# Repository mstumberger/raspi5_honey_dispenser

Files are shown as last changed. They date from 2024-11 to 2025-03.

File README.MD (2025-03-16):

# Raspberry PI 5 honey dispenser

# Material

| Part | Price  | URL |
|---|---|---|
| 3D printed parts | ~5€ | https://github.com/mstumberger/raspi5_honey_dispenser/tree/master/stl |
| Raspberry pi 5 | 76.19€ | https://si.farnell.com/raspberry-pi/rpi5-8gb-single/raspberry-pi-5-model-b-8gb-2-4ghz/dp/4256000 |
| MicroSD card 32GB | 12.90€ | https://si.farnell.com/multicomp-pro/ts32gusd420t-mcp/mircosd-card-32gb-raspberry-pi/dp/3879376  |
| Power supply | 12.48€ | https://si.farnell.com/raspberry-pi/sc1157/power-supply-usb-c-5-1v-5a-black/dp/4263045 |
| USB Extension cable 0.3m | 6.5€ | https://www.aliexpress.com/item/1005003488021890.html |
| 5" touch screen | 27.94€ | https://www.aliexpress.com/item/1005007314274603.html |
| 90° HDMI cable (conn. A2, D2, cable 30cm) | 9.09€  | https://www.aliexpress.com/item/1005005945873056.html |
| 90° USB cable (AMUP-V8UP, 30CM) | 6.57€  | https://www.aliexpress.com/item/1005005978243043.html |
| 5kg Load Cell with HX711 Amplifier | 5.75€  | https://www.aliexpress.com/item/1005005990685261.html |
| 10x 2.54MM Pitch 30CM Dupont Line Wire | 3.19€  | https://www.aliexpress.com/item/1005005924705004.html |
| Connectors for motor connection | 5.21€  | https://www.aliexpress.com/item/1005004891694780.html |
| Connection wire 22AWG (1/3) | 6.08€  | https://www.aliexpress.com/item/1005006516374385.html |
| MG996R Servo motor | 5.35€  | https://www.aliexpress.com/item/1005007552788835.html |
| Piezzo buzzer | 0.23€  | https://www.aliexpress.com/item/1005006260328559.html |
| PWM Cooling Fan | 7.86€  | https://www.aliexpress.com/item/1005004219041650.html |
| RGB LED | 0.04€  | https://www.aliexpress.com/item/1005005990835193.html |
| SMD R150 and 2x R33 | 0.01€  | https://www.aliexpress.com/item/1005006823361841.html |
| PCB Proto-board | 0.30€  | https://www.aliexpress.com/item/1005006665029598.html | 
| 8x M2.5 Brass Hot Melt Nut Insert + bolt  | ~0.18€ | https://www.aliexpress.com/item/1005006760493119.html |

Total costs:

    ~190.87€

# Wiring

-	HX711 - GND 39, VCC 17, DT 40, SCK 38 (Weight)
-	Servo - GND 6, VCC 2, Signal 12 (Dosing)
-	Fan - GND 9, VCC 4 (PWM fan)	
-   Piezzo - Signal 36 (Audio Signal)
-	RGB LED - GND 14, Green 16, Blue 15, Red 13

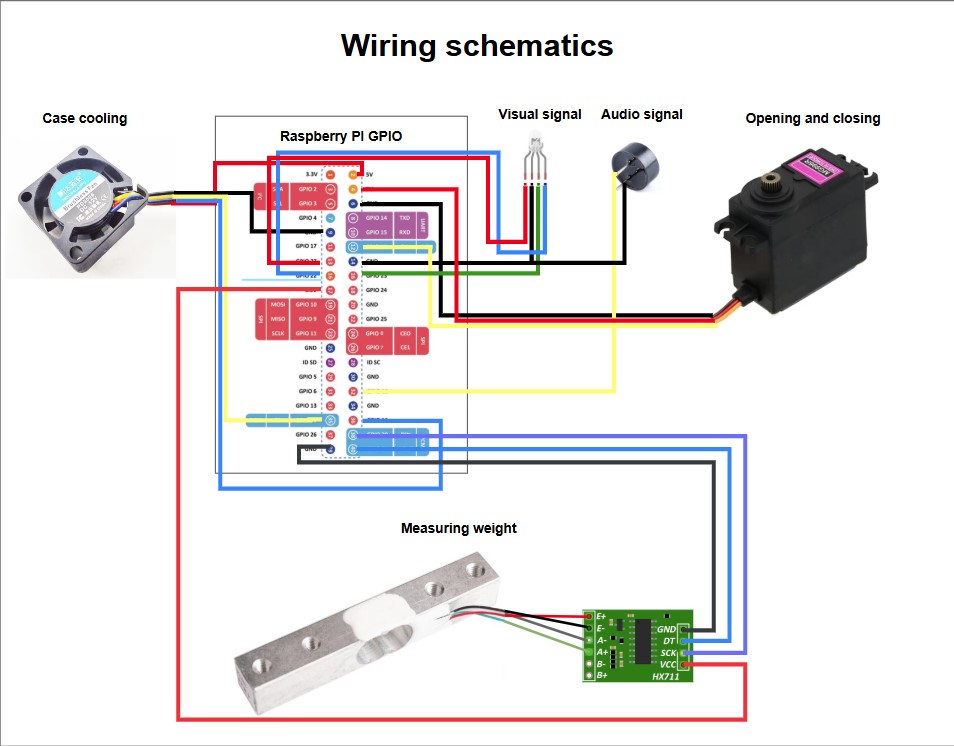
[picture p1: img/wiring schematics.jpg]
schematics


# Assembly instructions

1. Print STL Files for all components.
2. Insert Brass Insert Nuts into mounting locations on Raspberry Pi 5, signalization proto-board, HX711 amplifier, and display holder.
3. Solder Components: Attach the Piezo and RGB LED to the proto-board, create a common ground, and use connectors for wiring to the Raspberry Pi.
4. Mount Touchscreen: Connect the USB and HDMI cables to the touchscreen, then mount it onto the "stl/Scale - Display holder v5.stl" using 4 M2.5 screws.
5. Prepare Servo Motor Wiring: Solder 3 wires to a male connector for controlling the servo motor, then place the connector into the display holder.
6. Install USB-C Extension: Mount the USB-C extension onto the display holder using provided screws.
7. Mount Load Cell: Attach the load cell to the display holder at the designated mounting point, ensuring the correct orientation. Also attach Scaling surface to the other end of the load cell.
8. Wire Connection: Route and connect the cables inside the housing to the HX711 amplifier, securing them with M2.5 screws.
9. Prepare MicroSD Card: Load Raspbian OS onto the microSD card and insert it into the Raspberry Pi card slot.
10. Install Raspberry Pi: Place the Raspberry Pi into its dedicated space in the holder and secure it with M2.5 screws. Connect the microHDMI and USB-C cables.
11. Connect Display Cables: Route the USB cable for the touch display through the designated space in the cover, then place the cover on the scale base, ensuring it clicks into place.
12. Power On: Connect the USB and power adapter to the scale, plug the power adapter into a socket, and wait for the Raspberry Pi to boot.
13. Prepare Servo Motor Cable: Solder two female connectors to the servo motor control cable.
14. Connect to Lid Adapter: Cut the servo motor wires, solder them to the male connector fixed in the "stl/Lid adapter - top.stl."
15. Attach Lid Adapter: Use two nuts and bolts to secure the lid adapter to the honey dispenser.
16. Install Servo Motor Handles: Attach the large handle to the servo motor adapter and secure it vertically. Fix the small handle by drilling a hole and using a screw.
17. Disconnect Large Handle for initial installation.
18. Motor Calibration: Once the application starts and the motor moves to position 0, reattach the large handle.
19. Calibrate Scale: Calibrate the scale using a known weight to ensure accuracy.
20. Start Honey Dispensing: Once calibration is complete and saved, you can begin dispensing honey

schematics

## Install
This script will automatically:
- apply patch for Raspberry PI 5 HX711 library,
- install dependencies,
- create desktop and menu entry and start the application

```console
pi@raspberrypi:~ $ git clone --depth=1 https://github.com/mstumberger/raspi5_honey_dispenser.git honey_dispenser
pi@raspberrypi:~ $ cd honey_dispenser
pi@raspberrypi:~/honey_dispenser $ chmod +x install_and_start.sh
pi@raspberrypi:~/honey_dispenser $ ./install_and_start.sh
```

## Manual Install

- Set rpi to performance mode:

```console
echo performance | sudo tee /sys/devices/system/cpu/cpu*/cpufreq/scaling_governor
```

- [lgpio-dev](http://abyz.me.uk/lg/index.html) is required to be installed. It may be available to you via apt:

```console
sudo apt-get install -y liblgpio-dev
```
If it is not available, manually build and install it by following the instructions [here](https://abyz.me.uk/lg/download.html#Download&Install).

- Install C++ dependency for python library

```console
pi@raspberrypi:~ $ git clone --depth=1 https://github.com/endail/hx711
pi@raspberrypi:~ $ cd hx711
```

For RPi 5 the expansion header GPIO pins are now on /dev/gpiochip4 instead of /dev/gpiochip0. [endail/hx711/issues/85](https://github.com/endail/hx711/issues/85#issuecomment-2129032985)

```console
pi@raspberrypi:~/hx711 $ cd src
pi@raspberrypi:~/hx711/src $ sed -i 's/Utility::openGpioHandle(0)/Utility::openGpioHandle(4)/g' HX711.cpp
pi@raspberrypi:~/hx711/src $ cd ..
```

```console
pi@raspberrypi:~/hx711 $ make && sudo make install
```

Source: [Raspberry Pi HX711 C++ Library Readme](https://github.com/endail/hx711/blob/master/README.md)

- clone application create virtual environment and install python dependencies

```console
pi@raspberrypi:~ $ git clone --depth=1 https://github.com/mstumberger/raspi5_honey_dispenser.git honey_dispenser
pi@raspberrypi:~ $ cd honey_dispenser
pi@raspberrypi:~/honey_dispenser $ python3 -m venv venv
pi@raspberrypi:~/honey_dispenser $ source venv/bin/activate
(venv) pi@raspberrypi:~/honey_dispenser $ pip3 install .
(venv) pi@raspberrypi:~/honey_dispenser $ deactivate
```

### Run

```console
pi@raspberrypi:~ $ honey_dispenser/venv/bin/dispenser
```

### Cooling Service

1. Create a Systemd Service

Copy service/fan_controller.service to /etc/systemd/system/fan_controller.service:
    
    sudo cp service/fan_controller.service /etc/systemd/system/fan_controller.service

2. Enable the Service

Run the following commands:

    sudo chmod +x /home/pi/fan_controller.py  # Ensure it's executable
    sudo systemctl daemon-reload  # Reload systemd
    sudo systemctl enable fan_controller.service  # Enable service on boot
    sudo systemctl start fan_controller.service  # Start the service now

3. Check if the service is running:

    sudo systemctl status fan_controller.service

Or to view live logs:

    journalctl -u fan_controller.service -f

### Tkiter application service

1. Create a Systemd Service

Copy service/tkinter_app.service to /etc/systemd/system/tkinter_app.service:

    sudo cp service/tkinter_app.service /etc/systemd/system/tkinter_app.service

2. Enable the Service

Run the following commands:

    sudo systemctl daemon-reload  # Reload systemd
    sudo systemctl enable tkinter_app.service  # Enable service on boot
    sudo systemctl start tkinter_app.service  # Start the service now

3. Check if the service is running:

    sudo systemctl status tkinter_app.service

Or to view live logs:

    journalctl -u tkinter_app.service -f

4. Stop running service:

    sudo systemctl stop tkinter_app.service

# Shutdown

To allow passwordless shutdown, you can edit the sudoers file:

    sudo visudo

Add the following line :

    pi ALL=(ALL) NOPASSWD: /sbin/shutdown

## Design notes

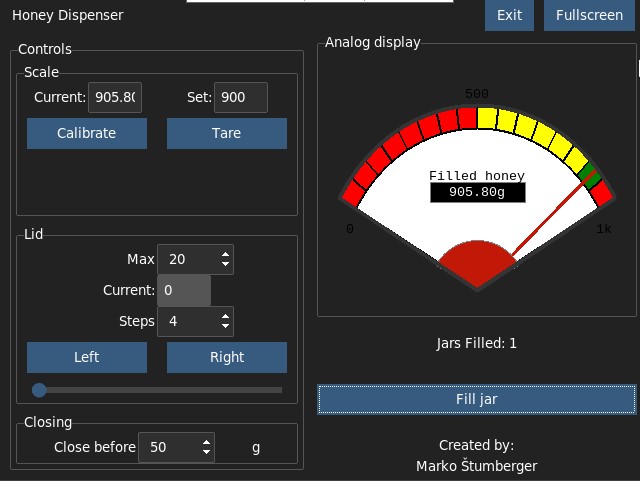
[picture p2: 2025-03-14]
img/dispenser_gui.jpg

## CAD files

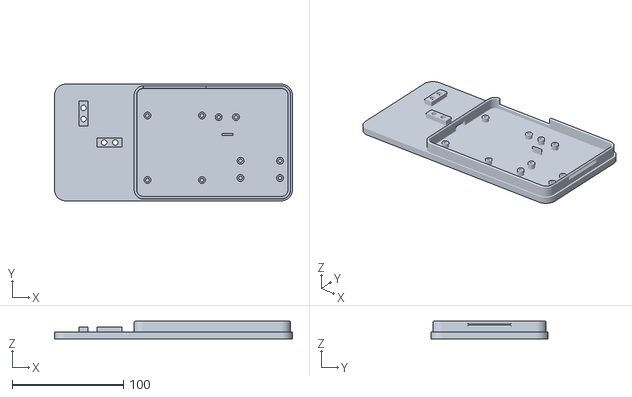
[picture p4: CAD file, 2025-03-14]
stl/Scale - Base v5.stl
214.0 x 105.0 x 16.0

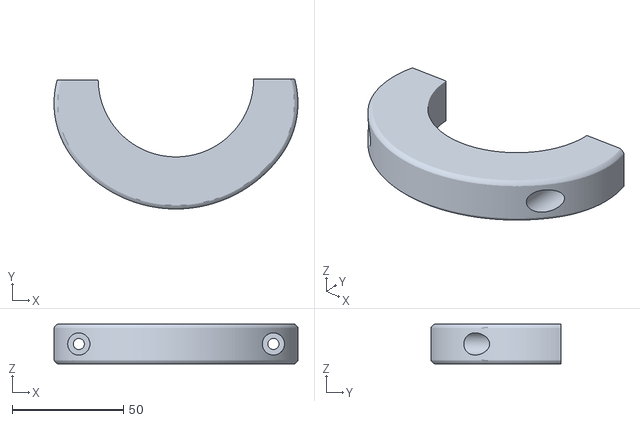
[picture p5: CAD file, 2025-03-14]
stl/Lid adapter - bottom.stl
109.9 x 58.5 x 18.0

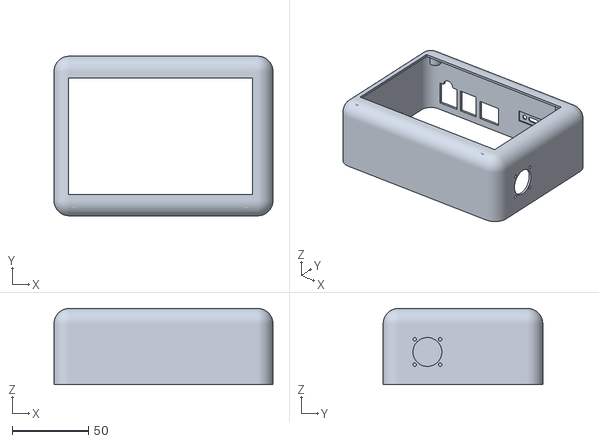
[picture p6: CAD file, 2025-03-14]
stl/Scale - Display holder v5.stl
144.0 x 105.0 x 50.0

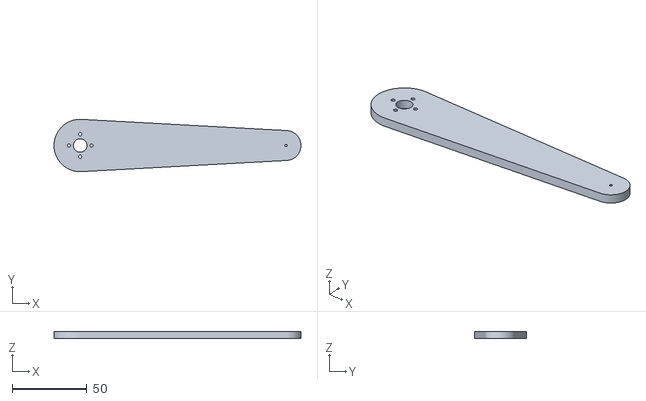
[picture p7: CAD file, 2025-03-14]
stl/Lid adapter - big handle.stl
165.0 x 35.0 x 5.00

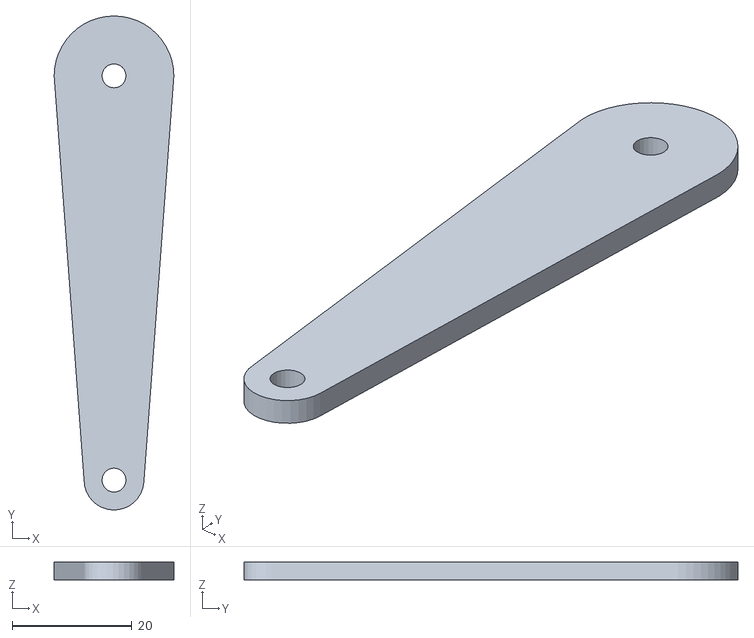
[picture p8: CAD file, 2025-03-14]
stl/Lid adapter - small handle.stl
20.0 x 82.5 x 3.00

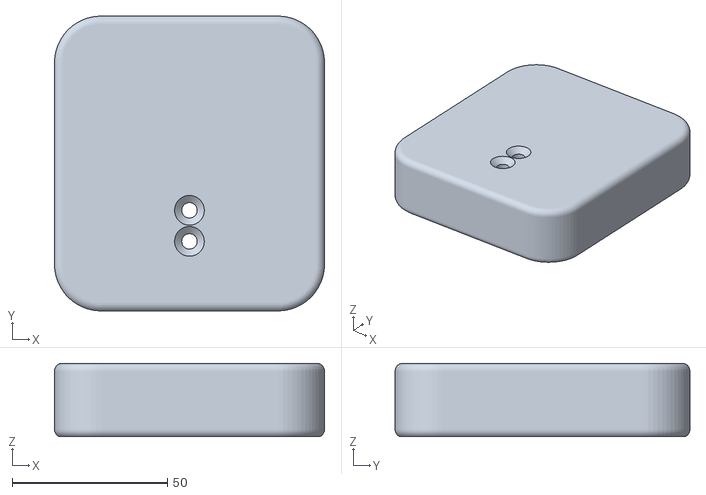
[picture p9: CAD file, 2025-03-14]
stl/Scale - Scaling surface v5.stl
87.0 x 95.0 x 23.7

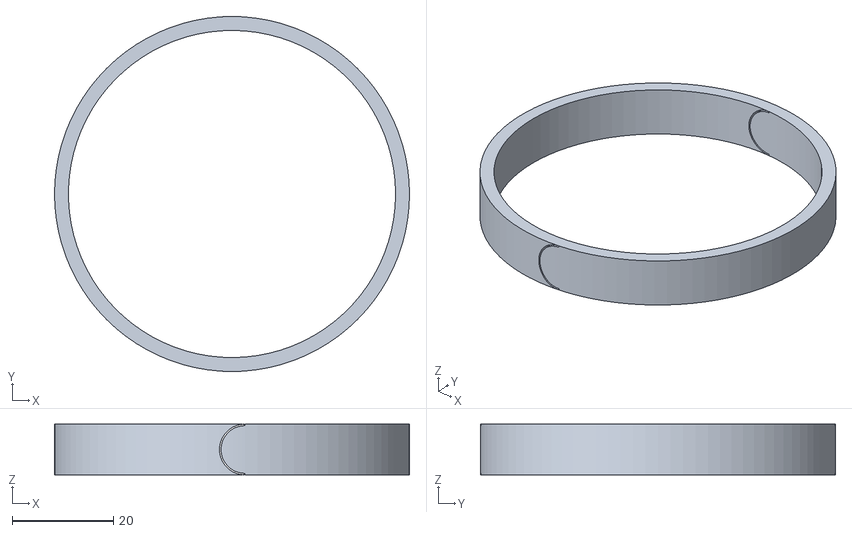
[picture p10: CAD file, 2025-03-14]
stl/Lid adapter - fitting.stl
70.0 x 70.0 x 10.0

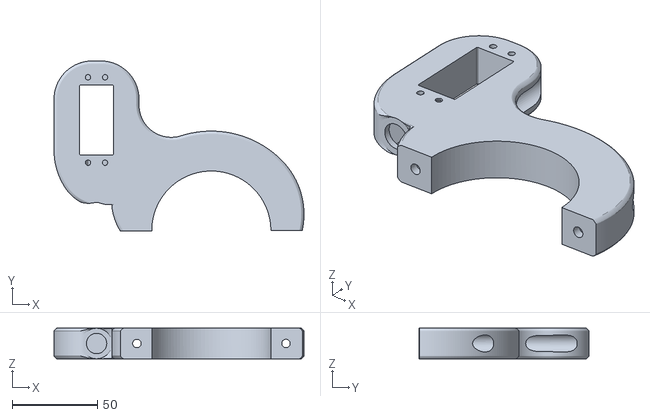
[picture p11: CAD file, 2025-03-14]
stl/Lid adapter - top.stl
146.9 x 100.0 x 18.0

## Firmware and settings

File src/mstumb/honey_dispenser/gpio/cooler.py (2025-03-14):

import os
import time
import threading
from collections import deque

try:
    import RPi.GPIO as GPIO
except ModuleNotFoundError:
    print("Using noop GPIO")
    from mstumb.honey_dispenser.gpio.noop import GPIO

FAN_PWM_PIN = 19  # PWM control pin
FAN_TACH_PIN = 16  # Tachometer pin (for RPM measurement)
TEMP_MIN = 55  # Temperature to start fan (°C)
TEMP_MAX = 75  # Temperature for full speed (°C)
TEMP_HISTORY_SIZE = 3  # Number of temperature readings to average


class CoolerController(threading.Thread):
    def __init__(self, pwm_pin=FAN_PWM_PIN, tach_pin=FAN_TACH_PIN, pwm_freq=10000, interval=5):
        """Initialize fan controller with PWM and RPM monitoring"""
        super().__init__()  # Initialize the Thread base class
        self.pwm_pin = pwm_pin
        self.tach_pin = tach_pin
        self.pwm_freq = pwm_freq
        self.interval = interval
        self.pulse_count = 0
        self.running = False
        self.temp_history = deque(maxlen=TEMP_HISTORY_SIZE)  # Store last 3 temperature readings

        GPIO.setmode(GPIO.BCM)
        GPIO.setup(self.pwm_pin, GPIO.OUT)
        GPIO.setup(self.tach_pin, GPIO.IN, pull_up_down=GPIO.PUD_UP)

        # Set up PWM
        self.fan = GPIO.PWM(self.pwm_pin, self.pwm_freq)
        self.fan.start(0)  # Start fan off

        # Set up tachometer interrupt
        GPIO.add_event_detect(self.tach_pin, GPIO.FALLING, callback=self.count_pulse)

    def count_pulse(self, channel):
        """Counts pulses from the fan's tachometer output"""
        self.pulse_count += 1


    def get_cpu_temp(self):
        """Reads the CPU temperature"""
        temp = os.popen("vcgencmd measure_temp").readline()
        return float(temp.replace("temp=", "").replace("'C\n", ""))

    def calculate_fan_speed(self, temp):
        """Maps temperature to PWM duty cycle (0-100%)"""
        if temp < TEMP_MIN:
            return 0
        elif temp > TEMP_MAX:
            return 100
        else:
            return (temp - TEMP_MIN) / (TEMP_MAX - TEMP_MIN) * 100

    def get_rpm(self):
        """Calculates RPM from tachometer pulse count"""
        pulses = self.pulse_count
        self.pulse_count = 0  # Reset counter after reading
        rpm = (pulses / 2) * 60  # Each revolution = 2 pulses
        return rpm

    def update_fan_speed(self):
        """Updates the fan speed based on the average of the last three temperature readings"""
        temp = self.get_cpu_temp()
        self.temp_history.append(temp)  # Store new temperature reading

        if len(self.temp_history) < TEMP_HISTORY_SIZE:
            avg_temp = temp  # Not enough readings yet, use the current temp
        else:
            avg_temp = sum(self.temp_history) / len(self.temp_history)

        speed = self.calculate_fan_speed(avg_temp)
        self.fan.ChangeDutyCycle(speed)
        rpm = self.get_rpm()
        print(f"Temp: {temp}°C (Avg: {avg_temp:.1f}°C) -> Fan Speed: {speed:.1f}% -> RPM: {rpm:.1f}")

    def run(self):
        """Main loop to monitor temperature and adjust fan speed"""
        self.running = True
        try:
            while self.running:
                self.update_fan_speed()
                time.sleep(self.interval)
        except KeyboardInterrupt:
            self.cleanup()

    def stop(self):
        """Stops the fan control loop"""
        self.running = False

    def cleanup(self):
        """Stops the fan and cleans up GPIO"""
        self.fan.ChangeDutyCycle(0)
        self.fan.stop()
        # GPIO.cleanup()
        print("Fan control stopped. GPIO cleaned up.")


# Example usage
if __name__ == "__main__":
    fan_controller = CoolerController(interval=5)
    fan_controller.start()  # Start the thread

    # Main thread can continue doing other work
    try:
        while True:
            time.sleep(1)
    except KeyboardInterrupt:
        fan_controller.cleanup()  # Clean up GPIO

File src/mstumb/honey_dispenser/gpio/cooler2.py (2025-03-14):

import os
import time
import lgpio

FAN_PWM_PIN = 19   # PWM control pin (BCM)
FAN_TACH_PIN = 16  # Tachometer pin (BCM)
TEMP_MIN = 55  # Temperature to start fan (°C)
TEMP_MAX = 80  # Temperature for full speed (°C)
PWM_FREQ = 10000  # 25 kHz

class CoolerController:
    def __init__(self, pwm_pin, tach_pin, pwm_freq=PWM_FREQ):
        """Initialize fan controller with PWM and RPM monitoring"""
        self.pwm_pin = pwm_pin
        self.tach_pin = tach_pin
        self.pwm_freq = pwm_freq
        self.pulse_count = 0

        # Initialize lgpio chip
        self.h = lgpio.gpiochip_open(0)
        lgpio.gpio_claim_output(self.h, self.pwm_pin)
        lgpio.tx_pwm(self.h, self.pwm_pin, self.pwm_freq, 0)  # Start at 0% duty cycle

        # Set up tachometer input
        lgpio.gpio_claim_input(self.h, self.tach_pin)
        lgpio.callback(self.h, self.tach_pin, lgpio.RISING_EDGE, self.count_pulse)

    def count_pulse(self, chip, gpio, level, timestamp):
        """Counts pulses from the fan's tachometer output"""
        self.pulse_count += 1

    def get_cpu_temp(self):
        """Reads the CPU temperature"""
        temp = os.popen("vcgencmd measure_temp").readline()
        return float(temp.replace("temp=", "").replace("'C\n", ""))

    def calculate_fan_speed(self, temp):
        """Maps temperature to PWM duty cycle (0-100%)"""
        if temp < TEMP_MIN:
            return 0
        elif temp > TEMP_MAX:
            return 100
        else:
            return (temp - TEMP_MIN) / (TEMP_MAX - TEMP_MIN) * 100

    def get_rpm(self):
        """Calculates RPM from tachometer pulse count"""
        pulses = self.pulse_count
        self.pulse_count = 0  # Reset counter after reading
        rpm = (pulses / 2) * 60  # Each revolution = 2 pulses
        return rpm

    def update_fan_speed(self):
        """Updates the fan speed based on CPU temperature"""
        temp = self.get_cpu_temp()
        speed = self.calculate_fan_speed(temp)
        lgpio.tx_pwm(self.h, self.pwm_pin, self.pwm_freq, speed)  # Update PWM duty cycle
        rpm = self.get_rpm()
        print(f"Temp: {temp}°C -> Fan Speed: {speed:.1f}% -> RPM: {rpm:.1f}")

    def run(self, interval=5):
        """Main loop to monitor temperature and adjust fan speed"""
        try:
            while True:
                self.update_fan_speed()
                time.sleep(interval)
        except KeyboardInterrupt:
            self.cleanup()

    def cleanup(self):
        """Stops the fan and cleans up GPIO"""
        lgpio.tx_pwm(self.h, self.pwm_pin, self.pwm_freq, 0)  # Stop fan
        lgpio.gpiochip_close(self.h)
        print("Fan control stopped. GPIO cleaned up.")

# Create an instance of the FanController and run it
if __name__ == "__main__":
    fan_controller = CoolerController(FAN_PWM_PIN, FAN_TACH_PIN)
    fan_controller.run()

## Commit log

2024-11-09 Initial commit - project structure, main window, top frame, readme, config file, gpio executor template, noop for developing gui on pc
2024-11-10 Fixed: install script Added: setup file, run from cmd command Updated: Readme
    [dispenser.py]
2024-11-10 Updated: setup with meta info, readme with install command fix Added: Noop function argument with default value
    [noop.py]
2025-03-14 Added STL models
    [Lid adapter - big handle.stl, Lid adapter - bottom.stl, Lid adapter - fitting.stl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]
2025-03-14 Changed to servo motor, added services to start at boot (#1)
2025-03-15 Gui improvements (#2)
    * Fixed setup and calibration
    * updated readme
    [buzzer.py, dispenser.py, noop.py]
2025-03-16 updated readme with material and assembly instructions
2025-03-16 Added wiring schematics
